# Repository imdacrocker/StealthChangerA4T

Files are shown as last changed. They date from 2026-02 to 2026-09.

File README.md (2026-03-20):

# StealthChangerA4T
A modified version of the A4T tool head and stealth changer dock and backplate, optimized for tool changing

First and foremost, this project is derived from many existing projects, let me give credit where it is due!

The backplate was modified from the official Draftshift Steath Changer:
https://github.com/DraftShift/StealthChanger

The A4T was modified from the Armchair Heavy Industries:
https://github.com/Armchair-Heavy-Industries/A4T

The dock is combined from multiple modular dock pieces, then heavily modified:
https://github.com/DraftShift/ModularDock

The sock was inspired by Nic335's design, but completely re-designed by me:
https://github.com/DraftShift/StealthChanger/tree/main/UserMods/Nic335/NH36Sock

The PCB mount was inspired by TheSin's mount:
https://github.com/DraftShift/StealthChanger/blob/main/UserMods/TheSin-/PCB36_Mount/PCBMount.stl

The APUS2 model was taken from the APUS2 Github:
https://github.com/Phaetus/APUS-2

The OptoTap model was taken from the OptoTap CAD:
https://github.com/VoronDesign/Voron-Tap/tree/main/OptoTap

The Nitehawk board and cable was taken from the Nitehawk CAD:
https://github.com/MotorDynamicsLab/Nitehawk-36
Though the cable was simplified by me to smooth out the cavity

The 3007 Fan Mount is my original design



So why this project?

I assembled my Stealth Changer using the Anthead tool head, as is often recommended.  But, I really wasn't very happy with that tool head.
It seems too complicated, has too many pieces, and is hard to work on.  Having to dis-assemble the entire tool head, to snug the hot end screws, was not my favorite project.  Plus, I was strugging with hot end cooling, as well as part cooling that was a little sub par.

I had previously used the A4T tool head, and really appreciated its simplicity and how solid it was.  Plus, it had better cooling.  

However, the published backplate for the A4T was hard to print.  The A4T was designed for the XOL carriage, and had mounting points that were really not neccessary when used with a Stealth Changer back plate.  That, and it did not have magnets built in.  There was a modified dock upright that used magnets, but I rather preffered a dock that did not use the uprights at all.

So, I began by updating the A4T, to flatten the back, and switch to heat set inserts in the body, rather than through bolts.  This allowed me to mount the screws from the backplate, since access is not an issue on the Stealth changer.
I then added 6 magnets, 4 in front, and 2 on the bottom, to lock the tool head in place nicely



Moving on to the dock, I took the existing modular dock, and merged it into a single body.  Modular is nice, but a single part is nicer.
I narrowed the dock body to 72mm, so I could fit 5 toolheads on my 300mm Voron.  I originally left the back adjuster separate, but ended up including that in the single piece as well.  I then updated the shape of the dock, to better fit the A4T, and to include the magnets.  I also opted for the Bambu style wiper.  I widened the attatching bolt spacing, and added an extra side support for the 2020 extrusion.

Originally, I had no upright support, but I found that with my LDO kit, the 2020 extrustion was too easy to twist.  This is probably not necessary on a setup that uses a solid bar that goes all the way across, but I definitey needed that support for my kit.  I include a left and a right, but you only really need one on the FAR left and FAR right dock, not every dock.

The dock is designed to print on the front face at a 45 degree angle.




Next, I updated the back plate.  I added a mounting point for the PCB, and added holes at the bottom to mount the A4T.  I also updated the chamfer, to not have any complete overhangs.  It prints quite nicely flat now, with no supports



On to the PCB mount.  I really liked the WWG2 for its simplicity, so that is what I used here.  I liked the idea of the sock mount, but I had always struggled getting it off.  I opted for a smooth support for the sock.



The sock was completely redesigned.  I wanted to be able to securely mount the sock to the PCB mount, but have it easy to un plug.  So I added 4 notches, that work perfect with small zip ties, to create a snug lock.  It is slotted in the back, to allow easy installation on your cable



Finally, I needed cooling for my Nitehawk.  The 3007 fans available for Raspberry Pi's were easy to get, and dirt cheap.  So I created a simple mount that is used in conjunction with the Nitehawk mount.  It also has a tab, that works with the lower zip tie, to hold the whole assemmbly snug.
This one requires some supports to print.  The supported surfaces don't seem to print very nicely, but that doesn't affect functionality



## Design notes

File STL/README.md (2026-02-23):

Print Settings

Since the files were pulled from a few different projects, there are a couple of caveats to the settings

First, you can use standard Voron settings for the line width and height

But the A4T was designed WITHOUT shrinkage in mind.  So you need to calibrate shrinkage, and use that in your slicer

The dock was cut from the shape of the A4T, so you will need to print that with shrinkage compensation as well

Second, the backplate was designed WITH shrinkage in mind.  So when you print that piece, it is expected that you will print it in ABS or ASA, with NO shrinkage compensation

The rest of the parts are not that picky, and can be printed with or without compensation

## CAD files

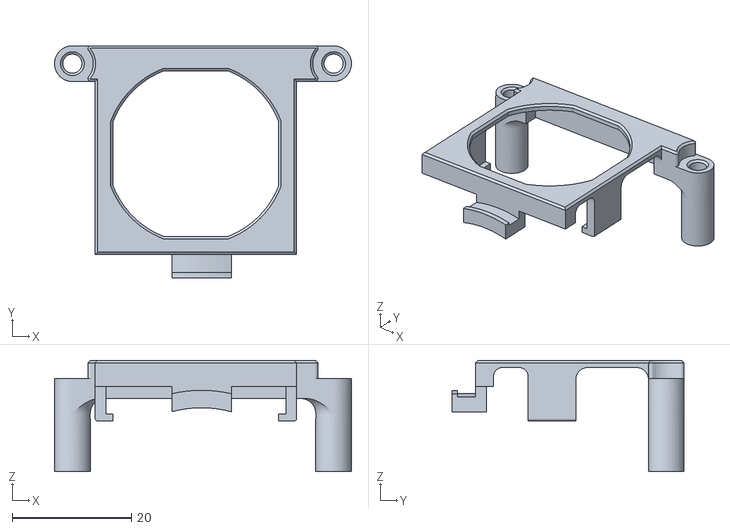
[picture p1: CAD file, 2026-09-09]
STL/3007_Fan_Bracket.stl
49.8 x 39.0 x 18.7

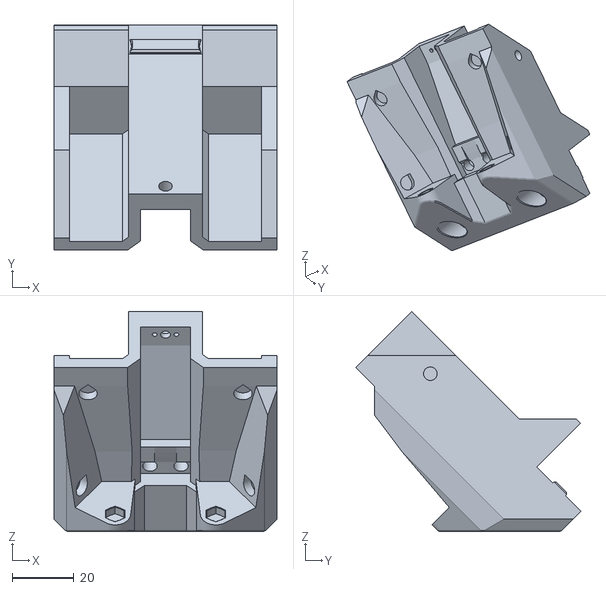
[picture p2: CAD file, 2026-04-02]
STL/Dock.stl
72.0 x 72.7 x 71.0

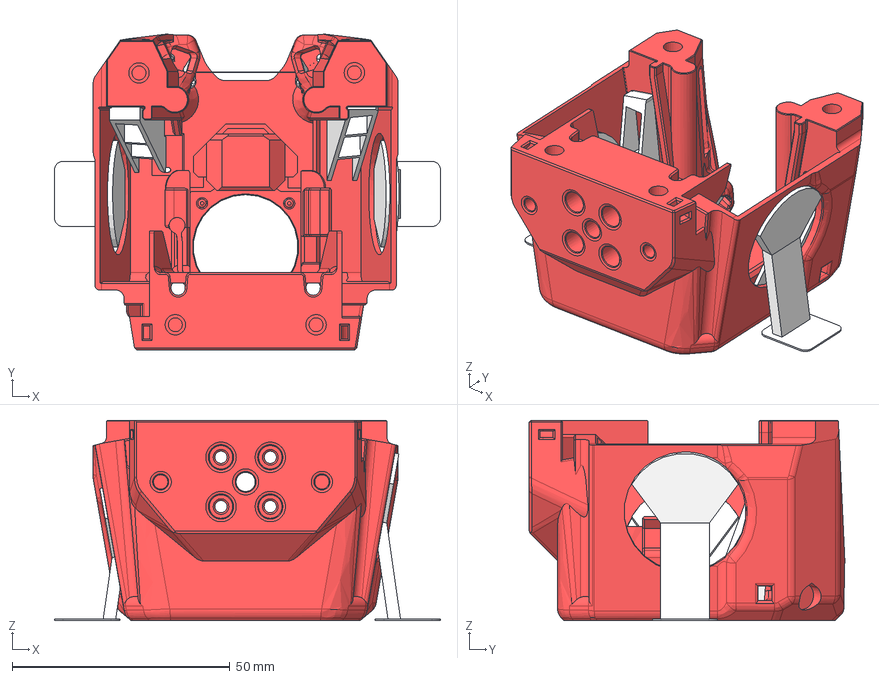
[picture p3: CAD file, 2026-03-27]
STL/A4T_Cowl_DragonUHF_Orbiter.step
88.6 x 72.4 x 46.0 mm
solid hexagons
outline hexagons
solid hexagons_1
Support_Fan-slot
solid hexagons_2
A4T Cowling - Dragon-Rapido UHF - G2-Orb Spacing [cw2-tap]
solid hexagons_3
solid hexagons_4
Support_Duct_Left
outline hexagons_1
solid hexagons_5
solid hexagons_6
solid hexagons_7
Support_Fan-slot_1
Support_Duct_Right

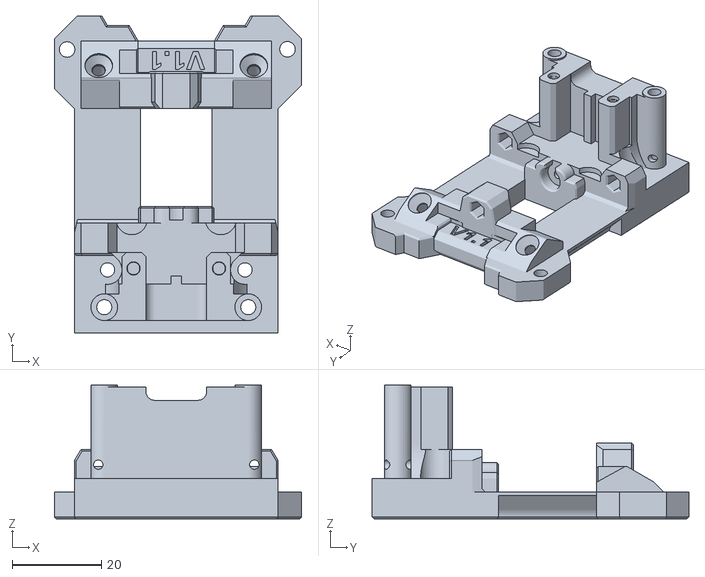
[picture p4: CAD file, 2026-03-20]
STL/Backplate.stl
55.4 x 71.0 x 30.0

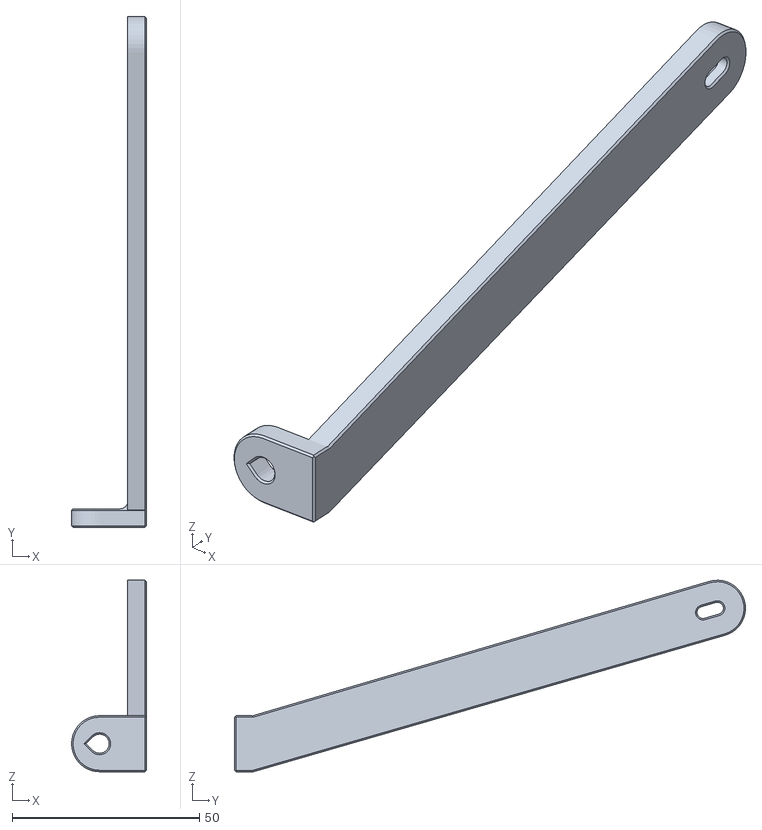
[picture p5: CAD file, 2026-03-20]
STL/Left Support.stl
20.0 x 136.4 x 51.2

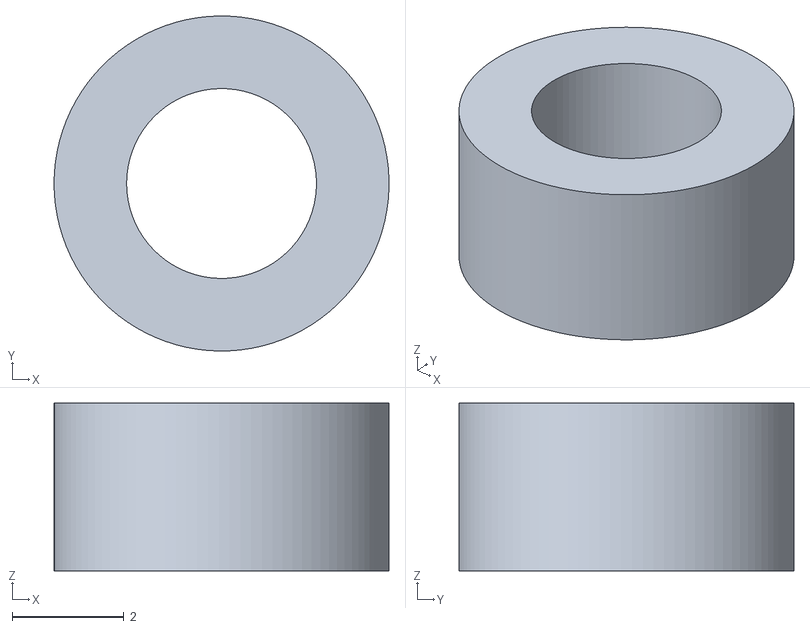
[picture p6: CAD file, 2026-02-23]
STL/3mm_Space_For_APUS2.stl
6.00 x 6.00 x 3.00

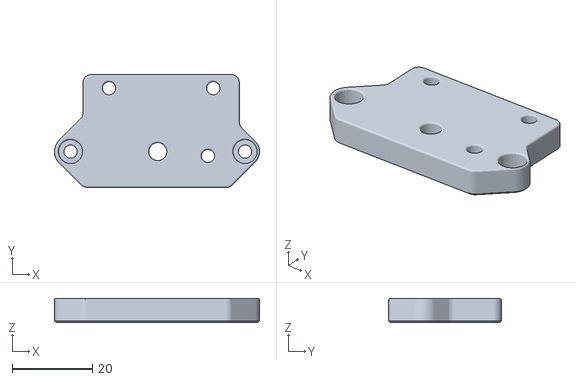
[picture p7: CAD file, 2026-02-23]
STL/APUS2_Sherpa_Adapter.stl
51.1 x 28.1 x 6.00

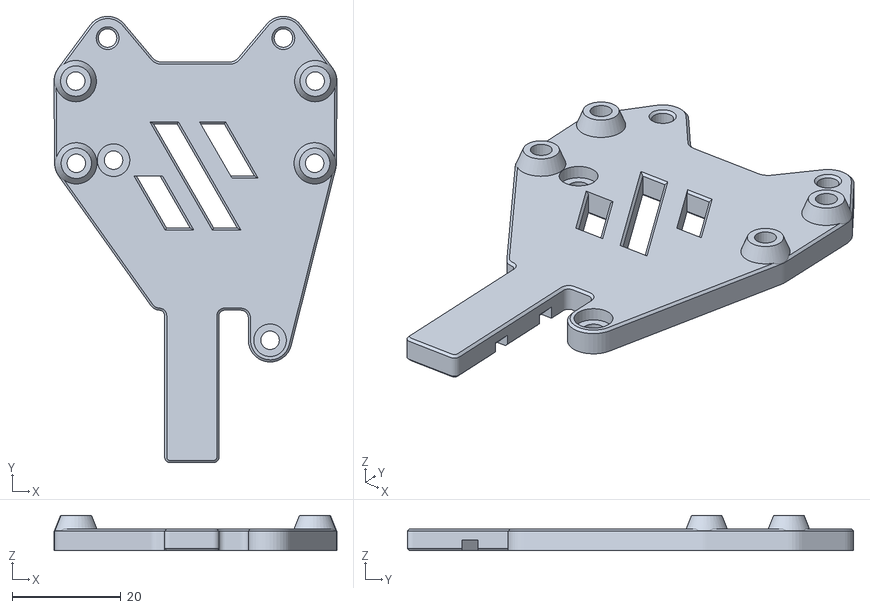
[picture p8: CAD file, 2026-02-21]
STL/PCB_Mount_APUS2.stl
52.0 x 82.0 x 6.50

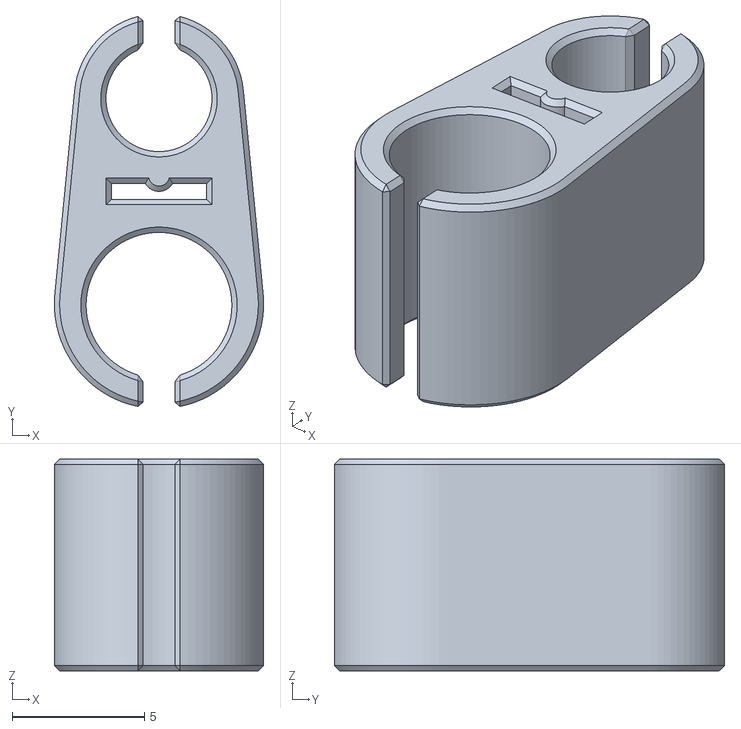
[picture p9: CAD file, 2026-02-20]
STL/[TPU]Inline_Clip.stl
7.90 x 14.7 x 8.00

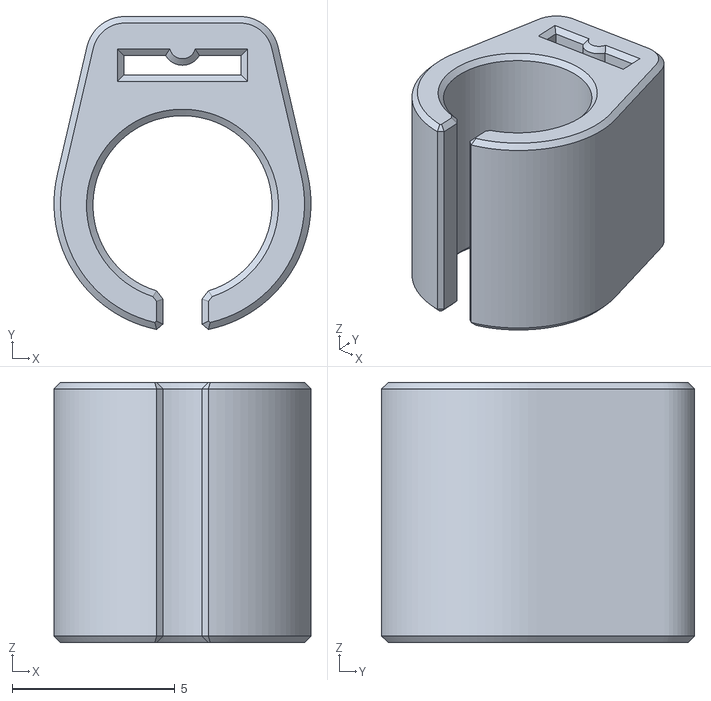
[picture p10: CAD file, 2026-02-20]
STL/[TPU]Inline_Clip_WireOnly.stl
7.90 x 9.62 x 8.00

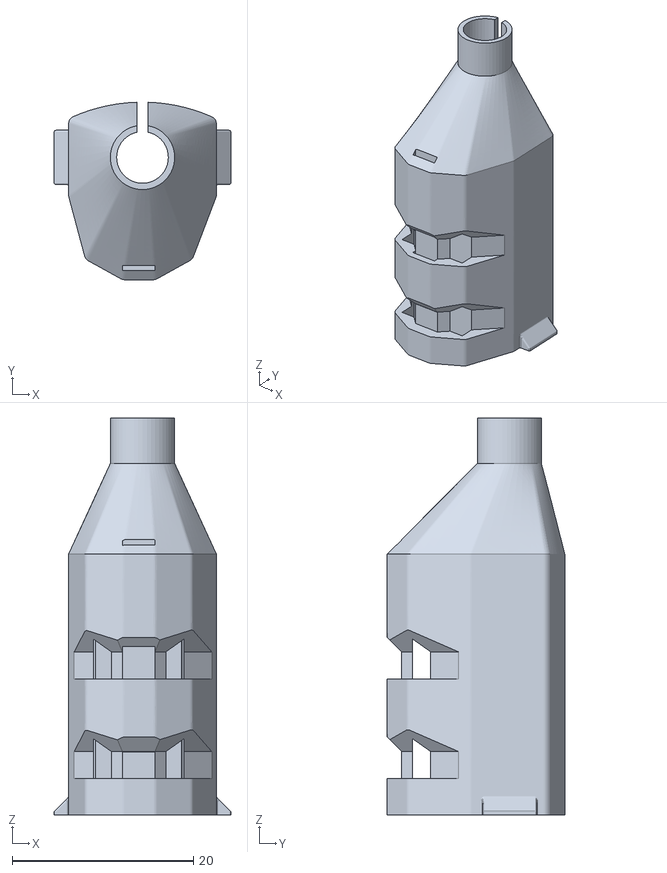
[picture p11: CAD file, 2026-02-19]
STL/[TPU]Sock.stl
19.5 x 19.6 x 43.8

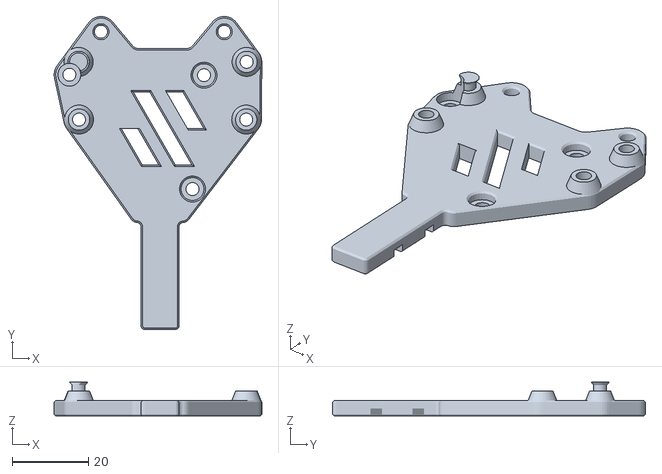
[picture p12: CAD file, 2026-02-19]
STL/PCB_Mount_WWG2.stl
54.4 x 82.0 x 8.90

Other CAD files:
STL/Right Support.stl

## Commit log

2026-02-18 Initial commit of CAD and STL files
    [3007_Fan_Bracket.stl, Backplate.stl, Dock.stl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]
2026-02-19 Fixed the side of the heat set inserts Added a pin for the lower PCB
    [PCB_Mount_WWG2.stl]
2026-02-19 Increased the size of the cavity for the plug Fixed a number of minor geometry errors
    [[TPU]Sock.stl]
2026-02-19 Updated the sock Fixed the geometry, and increased the plug cavity size Updated the PCB to fix the heat insert hole side, and added a pin for the lower slot
2026-02-19 Increased the height of the sock by 1 mm
    [[TPU]Sock.stl]
2026-02-20 Increased the spacer by 1mm
    [3007_Fan_Bracket.stl]
2026-02-20 Initial commit of clips
    [[TPU]Inline_Clip.stl, [TPU]Inline_Clip_WireOnly.stl]
2026-02-20 Increased the spacing on the fan bracket by 1mm Increased the height of the sock by 1mm
2026-02-21 Added PCB_Mount_APUS2 Updted 3007_Fan_Bracket to add a radius support in the corners Updated the Backplate to fix a hole that was too large for a heat set insert
    [3007_Fan_Bracket.stl, Backplate.stl, PCB_Mount_APUS2.stl]
2026-02-21 Added print supports for the front mounted magnet on the A4T
2026-02-23 Initial commit of the APUS2 adaption
    [3mm_Space_For_APUS2.stl, APUS2_Sherpa_Adapter.stl]
2026-02-23 Updated the clearance for the OptoTap
    [Backplate.stl]
2026-03-20 Initial commit of the upright dock supports
    [Left Support.stl, Right Support.stl]
2026-03-20 Updated the dock to hollow out the bottom, add a 3rd pair of magnets, and to integrate the back adjuster
    [Dock.stl]
2026-03-20 Updated the bottom parts of the backplate to shorten them, to go with the single piece dock
    [Backplate.stl]
2026-03-20 Fixed an issue where one of the fan bracket legs was 1mm too long
    [3007_Fan_Bracket.stl]
2026-03-20 Updated to add 2 more magnets at the front
    [A4T_Cowl_DragonUHF_Orbiter.step]
2026-03-20 Updated the dock, the backplate, fixed the fan bracket, and added 2 more magnets to the front
2026-03-27 Fixed a missing LED support in the cowl
    [A4T_Cowl_DragonUHF_Orbiter.step]
2026-04-02 Updated the dock clearances, and removed the back support, as it is now integrated
    [Dock.stl, Dock_Back_Support.stl]
